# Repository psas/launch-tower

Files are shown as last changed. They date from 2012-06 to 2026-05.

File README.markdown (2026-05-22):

PSAS Launch Tower Computer (LTC)
================================

PSAS has had three generations of launch tower computers:

- [LTC v1 (2005-2012)](http://psas.pdx.edu/Lv2LaunchTowerElectronics/)
   - PC-104+ 486 running Linux 2.4 talking CAN to PIC18F-based boards with relays and analog
   - Lucent "Wavelan" PCMCIA WiFi card
   - 12V SLA battery powered with 30W solar panel
   - Metal IP66 case on independent
- [LTC v2 (2012 - 2014)](http://psas.pdx.edu/GroundTeamHome/launch_tower_v2/)
   - Beagle board talking USB to Phidget relay and analog boards
   - Alpha WiFi board
   - Ethernet umbilical cord
   - 12V SLA battery powered with 30W solar panel
   - Medium sized plastic IP67 enclosure
- LTC v3
   - BeagleBone Black using GPIO and analog mounted on a single custom carrier PCB
   - 14.7V LiPo pack with solar charger.
   - Smaller case

This repo contains everything related to the launch tower computer
(LTC), with the exception of the userspace software, which is
contained in the [launch-tower-comm repo](https://github.com/psas/launch-tower-comm).

Contents
========

- doc
   - Documentation, what there is of it.

- eagle
   - Schematics and PCB layouts, made with [Eagle](http://www.cadsoftusa.com/).

- laser_cut_drawings
   - Line art of the power and ignition boards' mounting panels, suitable for use with a laser cutter.

- ltc3
   - Everything related to the design and manufacture of the third generation launch tower computer, LTC3.

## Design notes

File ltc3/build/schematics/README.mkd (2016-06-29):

# Launch Tower Computer III Schematics

This directory contains PDF schematics for each board in the LTC3
design.

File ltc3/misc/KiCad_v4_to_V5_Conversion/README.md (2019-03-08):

# KiCad v4 to V5 Conversion

This directory contains sed scripts used to convert LTC3's KiCad design
files from v4 to v5.

Conversion is a two-part process:

1. Create a complete sed script.  Start with the "base" sed script
   (suitable for any eeschema v4 files ) by appending rules for the
   conversion of local symbol names::

    cp eeschema_v4_to_v5_base.sed eeschema_v4_to_v5.sed
    (cd ../../kicad/libs/symbols/ && grep \$CMP *dcm) | sed -f make_sed_rules_for_local_symbols.sed >> eeschema_v4_to_v5.sed

2. Convert individual eeschema ``*.sch`` files::

    sed -f eeschema_v4_to_v5.sed $YOUR_EESCHEMA_FILE_HERE > $YOUR_EESCHEMA_FILE_HERE.v5

The resulting output is totally guaranteed to probably not be perfect,
usually because a previously-used stock symbol has changed slightly in
size, default orientation, etc.  Some post-conversion assembly may be
required.

Also note that the above example commands may well need to be adjusted
to suit your working environment ($PWD, etc.)

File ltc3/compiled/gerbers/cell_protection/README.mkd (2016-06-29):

# Cell Protection Gerbers

This directory contains Gerber design files for the LTC3 cell
protection board.

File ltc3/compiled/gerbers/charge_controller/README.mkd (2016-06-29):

# Charge Controller Gerbers

This directory contains Gerber design files for the LTC3 charge
controller board.

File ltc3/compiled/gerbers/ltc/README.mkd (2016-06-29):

# Launch Tower Computer Gerbers

This directory contains Gerber design files for the LTC3 main board.

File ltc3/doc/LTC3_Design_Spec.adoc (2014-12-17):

= PSAS Launch Tower Computer III Design Specification

FIXME: Feel free to make any additions or corrections.

== Abstract

The existing launch tower computer (LTC), the second major design
since the group's founding, is due for an overhaul.  It's only been
two years since LTC II was put into service, but there have been rapid
advances in available off-the-shelf technology, and our understanding
of what we need (and don't want) in an LTC has continued to evolve.

This document should be considered the source of authority for all
questions related to the design and implementation of the LTC III.

== Definitions

Computer::
  The single-board computer that comprises the core of the LTC.

Launch Tower Computer (LTC)::
  The entire system, including the enclosure, the single-board
  computer, the peripherals, etc.

== LTC II Review

=== The Good

* Safety interlocks!

* Solar charging.

* LiPo ignition battery.

=== The Bad

* http://www.phidgets.com/[Phidgets].  Expensive (relatively), fiddly,
  and require their own interface board.  Their software stack is
  thick and troublesome to install.

* The shore power DC-DC converter integrated with the power board was
  sorely inadequate.

* Lead-acid car batteries (LTC II's main power source) are bulky and
  heavy.

* The door covering the side bulkhead (power and arm switches) can't
  be closed when the shorting bar is in place.  The bar has to be
  stored elsewhere when the LTC not in use.

* The PowerPole connectors on the bottom bulkhead are too deeply
  recessed, located too close together, and poorly labeled.

== LTC III Goals

* Simplify!  LTC II has too many circuit boards, too many wires, too
  many everything.  It's difficult to service most of LTC II's
  components without major disassembly.  Peripherals (sensors, relays,
  etc.) should be contained on a single custom PCB.

* Make it smaller.  Reduce the size of the boards, batteries, and
  potentially even the enclosure.

* Replace LTC II's plastic enclosure with a metal enclosure, for
  durability and RFI protection.

* Improve the enclosure-to-tower mounting apparatus;
  make it fast and easy to mount (and dismount) the enclosure to the
  tower (https://en.wikipedia.org/wiki/DIN_rail[DIN rail] mounting (or
  something similar).

* Strive for field-replaceable units (FRU) whenever possible.  FRUs
  can be swapped out with basic tools, in a minimum amount of time.

* Make it user-friendly (i.e., fool-proof).  Any member of PSAS
  should be able to achieve a high-level understanding of the LTC in a
  short amount of time.  Any member should be able to operate, and if
  necessary service, the LTC given suitable documentation.

* Conduct a thermal analysis.  Do we need an active cooling system to
  deal with the heat of a desert launch site?

== Requirements

=== Power Sources

All the ways the LTC can get the juice it needs.

* 12 VDC rail from main batteries.

* 12 VDC rail from photovoltaic panels.

=== Power Supplies

The power rails the LTC provides to its various peripherals.

* 5 VDC rail to power to computer, etc.

* 12 VDC rail to ignition battery charger.

* 24 VDC rail to shore power.

* Several external expansion power connectors; switchable by the
  computer.

=== Sensors

* Voltage sensors for each power rail.

* Temperature sensor for enclosure interior.

* Support for at least four relays.

* External USB-connected WiFi adapter for computer.

* Add second enclosure access panel.  Divide main power switch; and
  ignition arming switch, shorting bar, and fuse into separate panels.

=== User Interface

* Stand-alone voltmeters on the front panel, for each power rail.
  (Stand-alone meters have no dependency on the computer being
  booted.)

* Front panel LEDs indicating the status of each relay, and the
  rocket-ready status.

* Main power switch

* Ignition arming switch.

* Ignition shorting bar.

* Ignition fuse.

* Label all the things!  Components, connectors, switches, oh my!

=== External Connections

* Rocket umbilical.  Connection state should be detectable by the
  computer.

* Away box

* WiFi coax

* Distinct, keyed connectors for each external connection.  There
  should be no way to accidentally connect a data cable to a power
  outlet; or to reverse the polarity of a connector.

* Several Ethernet connectors that provide external access to the
  LTC's internal subnet, for debug and expansion purposes.

* Several expansion trigger switches, for computer control of cameras,
  etc.  Switches short two external inputs together.  Nate proposes
  1/8" phono connectors for these.

* Expansion Ethernet and power connectors can be paired up for use
  with passive PoE injectors, providing single-cable power and network
  support for off-board devices (e.g., weather station).

== Design

TODO: More words, please.

* BeagleBone Black SBC

* BBB flipped upside down and mated to peripheral board via pin
  headers.  A kilt, rather than a cape!

=== Power Sources

=== Power Supplies

=== Ignition Subsystem

=== Networking

* Internal Ethernet switch.

== References

http://kilobaser.com/blog/2014-07-15-beaglebone-black-gpios["BeagleBone
Black GPIOs"], KiloBaser.

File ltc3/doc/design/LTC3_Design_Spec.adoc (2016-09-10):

= Portland State Aerospace Society Launch Tower Computer 3 Design Specification
PSAS Avionics Team <psas-avionics@lists.psas.pdx.edu>
v0.5, 14 July 2016: DRAFT

:imagesdir: ./images

== Summary

This document is the source of authority for all questions related to
the design and implementation of the third PSAS Launch Tower Computer
(LTC3).  If the design of LTC3 doesn't conform to this document, then
either the design is incorrect, or the document needs to be updated!

== Power

=== Sources
LTC3 will get its power from a bench power supply while in the lab,
and photovoltaic panels and batteries while in the field.

Minimum input voltage is determined by the DC-DC converter supplying
the 19 VDC rail, which requires an overhead of 4 VDC.  At minimum, a
24 VDC supply capable of sourcing at least TODO 10 amps is required.
footnote:[Refer to Texas Instruments PTN78020[WH\] datasheet, Aug.
2011, page 10, "Input Voltage Considerations"]

=== Battery
LTC3 uses a 28.8V, 8s2p LiPo battery pack.  The 28.8V nominal voltage
enables the use of buck converters on all three DC power rails.
Configurable buck converters are cheap and plentiful, and have higher
efficiencies than the boost converters.  Furthermore, the 8s2p
configuration enables us to charge-balance individual cells.  The
downside is the need for a custom charging circuit, as most
off-the-shelf chargers are designed for 12V nominal MPPT and 4s cell
configurations.

==== TODO
* Based on assumptions: 90% efficiency, calc. 96W of power (a
  conservative estimate), 4 hours pure battery, we need a capacity of
  13.2Ah at 28.8V nominal.
* An 8s2p final configuration of 6.7 Ah cells would get
  us into our 4 hours.

==== Charge Controller
LTC3 uses the Linear Technologies LT8490, a switching buck/boost
regulator that integrates a charger and solar MPPT.  It is robust and
inexpensive.  Implementation of circuits based on the LT8490 are
somewhat complicated, but are a big win in terms of cost and system
flexibility.  The LT8490 can be powered with a wide range of input
voltages.  A single connctor can be used for either the solar panels
or 12V bench power supplies.

==== Battery Management and Cell Protection
LiPo cell protection is provided by a Texas Instruments bq77PL900
("bq").  The bq performs both battery balancing and protection
for up to 10 lithium-polymer cells.  Cell balancing and protection
prevent over-charging and -discharging of cells, giving the batteries
extra run time and lifespan.  It also prevents the overheating of
cells (a fire hazard), and prevents early capacity degradation.

===== Basic Function
The bq utilizes two different PMOS devices, which are turned on and
off by a microcontroller in the chip.  The bq senses battery cell
voltages through its VC pins (VC1-VC10).  When the battery's voltage
grows too high, the bq applies a voltage to the gates of the PMOS CHG
FETs, whose body diodes then prevent current from passing from the
input to the battery.  Likewise, when the battery's voltage drops too
low, the bq applies a voltage on the gates of the DSG PMOS FETs, whose
body diodes prevent current from passing from the battery to the load.
The charge pump built into the bq allows gate voltages to become high
enough for the CHG and DSG FETs to switch on and off.

===== Active Balancing
The bq uses active balancing in its design.  To do this, an integrated
NMOS in the chip is connected between two of the VC pins and turns on
when a certain voltage drops across it.  As a result, if one cell's
voltage is too much greater than another, the voltage drop across the
NMOS pushes current to the adjacent cell, and so on and so forth.  An
external 500Ω current-limiting resistor is used in conjunction with a
0.1μF filter capacitor.

===== Temperature Sensing
The temperature sensing feature of our design revolves around the TOUT
and TIN pins on the bq.  A voltage divider network is put in parallel
with a 10kΩ thermistor, which is taped to the battery pack.  The
thermistor's resistance decreases with increasing temperature (NTC).
When the battery pack gets hot, the voltage on the TIN pin becomes
low, turning off both the DSG and CHG FETs.  This prevents current
from flowing into our out of the battery, allowing it time to cool
off.  Once the temperature has stabilized, the bq resumes its regular
function.

===== Zero-Volt Charging
The zero-volt charging in our design is driven by another PMOS device
via the general-purposed open-drain ("GPOD") pin.  When voltage drops
below the supply voltage of the bq, the 0-V/precharge is enabled.
When this happens, the GPOD pin drives the 0-V/precharge FET (Q306 in
the LTC3 schematic).  When this FET is turned on, the CHG FET is
bypassed and current passes through the GPOD FET, allowing the battery
to charge.  When the voltage reaches a sustainable level for the bq to
operate, the GPOD FET is turned off and the CHG FET takes over.

===== Shutdown Mode
When undervoltage is detected, the bq goes into shutdown mode.  In
this mode, the DSG FET is turned off and all functions of the bq
cease.  To exit shutdown mode, a voltage greater than V~STARTUP~ must
be applied on the PACK+ pin.  This can be done in our system by
applying an output voltage from the LT8490 onto the PACK+ pin of the
bq.

=== DC Rails
LTC3 has three DC power rails:

* 5 VDC, for the Beaglebone, cape, and supporting logic
* 12 VDC, for the Ethernet switch and external device support
* 19 VDC, for rocket shore power

DC power rails are supplied by Texas Instruments PTN78020 switching
regulators.  The PTN78020 is a wide-input, wide-output, adjustable 6 A
regulator.  A PTN78020W converter is used for the 5 VDC rail;
PTN78020H converters are used for the 12 VDC and 19 VDC rails.

Based on the temperature derating curves in the PTN78020 datasheet
(rev. Aug. 2011), our worst case scenario is 4.0A load on the 12V DC
rail.  Fig. 21 in the datasheet indicates that the maximum ambient
temperature for such a load is approximately 55 °C.

.LTC3 DC Power Rails
[width="25%",frame="topbot",options="header"]
|===============================================
| V~out~ | I~min~ | I~typ~ | I~max~ | Part Num.
| 5.0    | ?      | 1.0    | 2.0    | PTN78020W
| 12.0   | ?      | ?      | 5.0    | PTN78020H
| 19.0   | ?      | 3.0    | 4.0    | PTN78020H
|===============================================

== Ignition Subsystem

The ignition system functions off three different relays.  The rocket,
which is connected with an umbilical cord, tells the LTC it is
prepared to launch by sending a "ROCKET_READY" signal to the LTC.
This activates a solid state relay (IC601) which pushes signal to the
following AND gate.

When the LTC sees the rocket ready signal and shore power, after a 5
second delay the second relay (K601) is triggered. Additionally, an
LED lights up indicating the rocket is "ready to launch," and assuming
the relay locks, the first light on the "BAKERCON" indicator will
light up.

The third relay is activated by the "ROCKET_IGNITE" pin from the
beaglebone on the LTC3. At this point the second light on the BAKERCON
idicator is lit.  When this signal is active, the third relay (K602)
closes and the system goes through a breaker arm, switch, and banana
jack to ensure launch is desired. When these three are connected, the
third and final BAKERCON indicator light is active.

The final step to launching the rocket is connecting the short-bar,
known as the launch key, to the away box.  When all of these
conditions have been met, the rocket will launch.

== Computer

The heart of LTC3 is a BeagleBone Black (BBB) single-board computer.

The BBB interfaces with the main board via a pair of 46-pin headers.
The main board appears to the BBB as a standard
http://beagleboard.org/cape["cape"].  The main board is on the bottom,
with the BBB mounted on top, upside-down.

=== Cape EEPROM Contents
TODO

== Sensors

LTC3 contains sensors to monitor the voltage and current sourced from
the photovoltaic panels; sourced from the main battery; and sunk on
the 5 VDC, 12 VDC, and 19 VDC rails.

Sensing of voltage, current and temperature alike is accomplished with
a pair of http://cds.linear.com/docs/en/datasheet/2991fd.pdf[Linear
Technologies LTC2991] _Octal I2C Voltage, Current, and Temperature
Monitor_ ICs.  One IC is dedicated to the LTC3's power sources, the
other to its sinks.  The ICs interface with the BeagleBone via an I2C
bus.

The temperature sensor integral to each LTC2991 will be used to
monitor the LTC3 main board.  An MMBT3904 NPN BJT connected to the
first LTC2991 (same IC used to monitor the power sources' voltage and
current) will be used to monitor the temperature of the main battery.

== Networking

* Internal Ethernet switch.

== External Device Support

LTC3 provides power and trigger support for four external devices
(e.g., cameras).

=== Power
Power is supplied through two-terminal Anderson Powerpole connectors,
available from the exterior of the LTC enclosure.  Current to each
connector is limited by a 2 A PPTC (PolyFuse).

Each power connector is controlled independently by the computer.
Photorelays, driven via GPIO through a MOSFET, are used to switch the
12 VDC rail to "Eurostyle" connectors mounted to the mainboard.
Common, 16-gauge stranded copper wire carries current from the
on-board connectors to the exterior-facing Powerpoles.

=== Triggers
Triggering is supplied through two-terminal TODO-CONNECTOR_TYPE
connectors, available from the exterior of the LTC enclosure.  Current
to each connector is limited by a 500mA A PPTC (PolyFuse).

Each trigger connector is controlled independently by the computer.
Photorelays, driven via GPIO through a MOSFET, are used to switch
either ground, or the 5 VDC rail, to "Eurostyle" connectors mounted to
the mainboard.  An on-board three-pin header is jumpered accordingly
to select the signal, whichever suits the device being triggered.

== User Interface

=== BAKERCON Hazard Gauge
Indicates at a glance how close ignition battery power is to the
rocket ignition outlet (to which the away box is connected).  Three
super-bright LED indicators are mounted to the enclosure exterior.
The first, yellow, lights when the ignition battery relay closes.  The
second, also yellow, lights when the rocket ignition relay closes.
The third, red, lights when power reaches the outlet.

The ignition sub-system is still fully functional when the 12V and 19V
supplies are disabled.  Thus, the BAKERCON is powered off of the 5V
supply.

== Physical

=== Printed Circuit Board
Trace widths must be sufficient minimize circuit impedance, and to
limit temperature rise.  Assume a maximum ambient temperature
(enclosure interior) of 60°C.  Maximum trace temperature rise should
be no more than 20°C.

=== External Connectors
IDEA: Powerpole connectors are mounted to the enclosure with
http://www.portableuniversalpower.com/anderson-autogrip/[Anderson
AutoGrips].  They're robust and inexpensive.

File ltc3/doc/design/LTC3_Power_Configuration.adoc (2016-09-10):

Does the LT8490 need to be reconfigured in order to take different
nominal input voltages?
  - pg. 14 - VINR needs to be grounded when the chip is getting direct
    DC input. (pg. 14) When panels are used, it needs to be hooked up
    to a resistor network to measure panel voltage.  This is
    implemented on pg. 35 - protection diodes are used to insulate VDC
    and VPanel, and a transistor shorts VINR when VDC is turned on.
  - We can ensure that no one uses the Lab and Panel supplies at the
    same time by just having a physical sliding cover.
	- DC current limiting for lab power

What configuration options does the LT8490 have? How should they be
configured?
  - Vmax selection - Based on the larger of panel Voc Max and DC max,
    we calculate an impedence network (pg. 14).  Minimum ckt input
    voltage is based on the selected Vmax; the lab power input and
    solar input both must exceed this level for efficient charging.
    (pg. 15).
	- Low-power mode - pg. 15
  - Simultaneous charging + discharging (in-situ; pg. 16) 
		- load connected directly across the battery terminals
    - disable charging time limits (CHARGECFG2 pin) 
    - the battery may draw below safe levels if it is charging and
      discharging simultaneously; build in protections?
  - Stage 2 charging threshold (pg. 17-18) - typically above nominal
    Vbatt; for LiPo cells this is usually 4.2V for 3.6V cell
    - Stage 3 is usually disabled for LiPo; the Stage 2 threshold is
      the most important limit for LiPo charging
	
- IMON_OUT, IMON_OUT capacitance (pg. 19, 20) - higher values reduce
  inductor current overshoot; lower values reduce ripple and give
  better ADC measurements. Need to separate pole at IMON_OUT from pole
  at Vc pin. Suggested value: 4.7 to 22nF
  - Input current limiting (pg. 19) should be panel max + 20%, but not
    dramatically higher than rated input
	- CHARGECFG1 options: (pg.20)
		- Temperature-compensated voltage limits
		- Enable/disable stage 3 (not typically used for LiPo)
    - For LiPo: Non-temperature-compensated, stage 3 disabled =
      grounded
  - CHARGECFG2 options: (pg. 22)
    - Enable/disable charge time limits: time limits not recommended
      for LiPo
    - Width of valid temp ranges (ratio > or < 0.5)
    - For LiPo: Narrow valid temp range, no time limits = grounded
  - Status/Fault LED configuration (pg. 26)
		- Use a resistor to limit STATUS current
		- FAULT self-limits on its own
		- Configure BB to interpret status/fault signals (pg. 25)
		- For our config: use resistor network as in Fig. 18
	- Switching configuration (pg. 29)
    - MODE pin above 2.3V = discontinuous conduction mode (DCM)
    - MODE below 0.4V = automatic CCM/DCM mode switching, automatic
      EXTVcc disconnect
    - For our config: tie MODE low - we typically want CCM
	- Low power mode (pg. 30)
		- Disabling: Rnlp can be connected between to FBIR.
		- For our config: no reason to disable low-power mode
	- Feedback resistor disconnect (pg. 31)
    - For our config: Feedback resistor disconnect is probably
      unnecessary for our application
    - We want voltage sensing even when batteries are not charging
    - Circuit as in fig. 26
	- EXTVcc disconnect mode (pg. 32)
    - For our config: EXTVcc disconnect is probably unnecessary
		- EXTVcc power draw is very low relative to our batteries
	- Remote batt V sensing (pg 32)
		- intended for low-voltage batteries charging at high currents
		- For our config: Not necessary.
	- Hot plugging (pg. 35)
    - We can either use the remote batt V sensing setup or use a
      staggered connector type
    - Word of god: don't worry about it for our application

- Inductor selection: see LT8705 datasheet for consideration (pg. 23)

- Board Layout checklist: see LT8705 datasheet (pg. 35)

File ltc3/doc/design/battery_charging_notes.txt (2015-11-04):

	-->

---------------------------------------------------------------------------

Welcome to Andy's Awesome program!  I hope you enjoy your time here!

---------------------------------------------------------------------------

What is maximum voltage that the solar panel will give?: 21.7

What is the stage 2 constant voltage you want for the batteries?: 33.6

What is the maximum input current from the solar panel?: 2.4

What is the maximum charging current?: 11.4

What is the maximum trickle current value?: 3

What would you like Rfbout2 to be? (choose between 4.99k - 49.9k ohms): 7000

What would ou like the switching frequency to be?:  250000

---------------------------------------------------------------------------------------------------------

Based on the specifications, the exact values you want should be:

Rfbin1 = 94725.966280

Rfbin2 = 7731.641101

Rdaci1 = 3318.425570

Rdaci2 = 16592.127852

Cdaci = 3.013477E-07

Rfbout1 = 203920.989595

Rfbout2 = 7000.000000

Rdac01 = 7899.283126

Rdac02 = 39496.415628

Cdac0 = 2.531875E-07

Rsense1 = 0.021042

Rsense2 = 0.004360

Rimonout = 92362.173038

Riow = 32975.744156

Rior = 3010.000000

---------------------------------------------------------------------------------------------------------

Based on the specifications, here are the closest real resistor values you can use:

Rfbin1REAL = 95300

Rfbin2REAL = 7680

Rdaci1REAL = 3320

Rdaci2REAL = 16500

CdaciREAL= 3.3E-07

Rfbout1REAL = 200000

Rfbout2REAL = 7150

Rdac01REAL = 8050

Rdac02REAL = 40200

Cdac0REAL = 2.7E-07

Rsense1REAL = 0.021

Rsense2REAL = 0.00432

RimonoutREAL = 93100

RiowREAL = 33200

RiorREAL = 3010

---------------------------------------------------------------------------------------------------------

Choose an inductor greater than 3.11562e-06 H

---------------------------------------------------------------------------------------------------------

-->

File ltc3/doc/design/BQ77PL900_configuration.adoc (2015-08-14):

-Eight-cell configuration: CNF2 and CNF0 shorted, CNF1 connected to VLOG through a 10kOhm resistor
-ZEDE to GND - normal operation for detection delay

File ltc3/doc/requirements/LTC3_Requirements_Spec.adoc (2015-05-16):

= Portland State Aerospace Society Launch Tower Computer III Requirements
PSAS Avionics Team <psas-avionics@lists.psas.pdx.edu>
v0.1, 27 January 2015: DRAFT

:imagesdir: ./images

== Summary

The launch tower computer (LTC) is an integral component in the
Portland State Aerospace Society (PSAS) launch vehicle complex.  It is
responsible for providing shore power to the rocket while it remains
on the launch pad; manages the ignition safety interlock system; and
ignites the rocket motor at launch time.

The existing launch tower computer, the second major design
since the founding of the http://psas.pdx.edu/[Portland State
Aerospace Society] (PSAS), is due for an overhaul.  It's only been two
years since LTC II was put into service, but there have been rapid
advances in available off-the-shelf technology, and our understanding
of what we need (and don't want) in an LTC has continued to evolve.

This document is the source of authority for all questions related to
the requirements of the LTC III.  If the document does not conform to
the known requirements, then either the requirements are incorrect, or
the document needs to be updated!

== LTC II Review

=== The Good
* Smaller and less heavy than LTC I

.The guts of LTC I
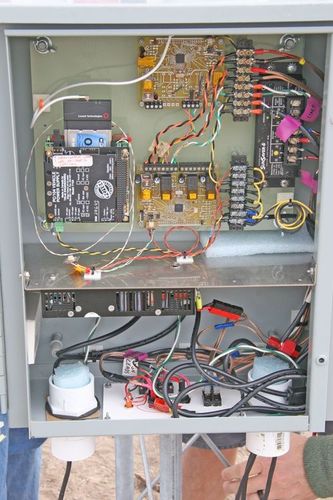
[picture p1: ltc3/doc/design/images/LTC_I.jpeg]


* Safety interlocks!

* Solar charging.

* LiPo ignition battery.

.LTC III ignition board and LiPo battery pack.
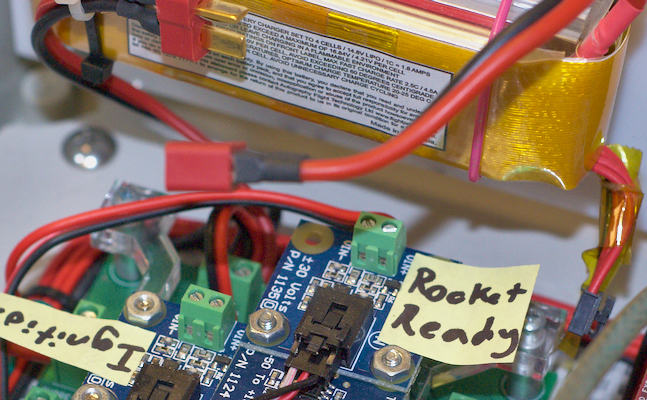
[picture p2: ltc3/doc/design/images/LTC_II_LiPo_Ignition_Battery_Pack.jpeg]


=== The Not So Good

* While smaller and lighter than LTV v1, still big and bulky and a
  pain to carry around.

* Complicated, heavily mod-wired, and difficult-to-trace wires all
  conspire to make debugging a real chore.

.The guts of LTC II
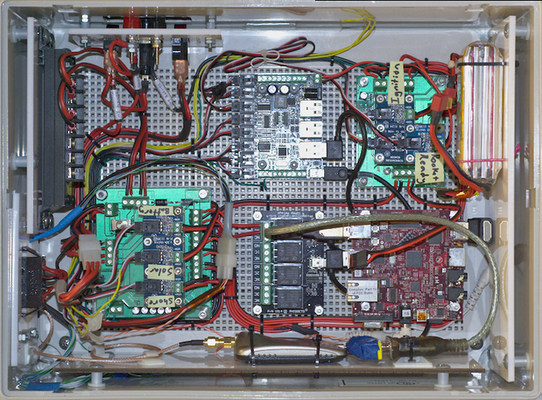
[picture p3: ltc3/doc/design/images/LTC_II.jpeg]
Photo of the interior of LTC II


* The shore power DC-DC converter integrated with the power board was
  sorely inadequate.

.LTC II power board.
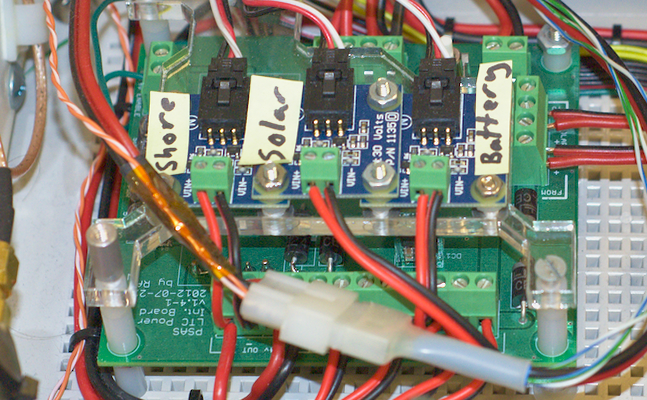
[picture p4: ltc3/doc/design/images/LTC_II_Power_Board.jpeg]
Photo of LTC II's power supply board.


* Lead-acid car batteries (LTC II's main power source) are bulky and
  heavy.

* http://www.phidgets.com/[Phidgets].  Expensive (relatively), fiddly,
  and require their own interface board.  Their software stack is
  thick and troublesome to install.

.LTC II Phidgets interface board.
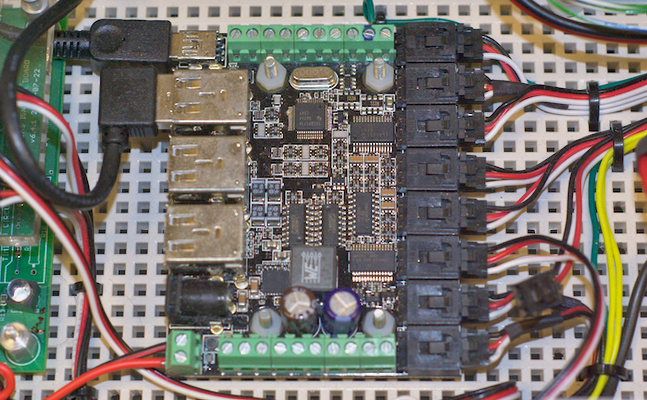
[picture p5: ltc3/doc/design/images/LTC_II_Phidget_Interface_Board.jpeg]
Photo of LTC II's Phidgets interface board.


* The door covering the side bulkhead (power and arm switches) can't
  be closed when the shorting bar is in place.  The bar has to be
  stored elsewhere when the LTC not in use.

.LTC II bulkhead access door.
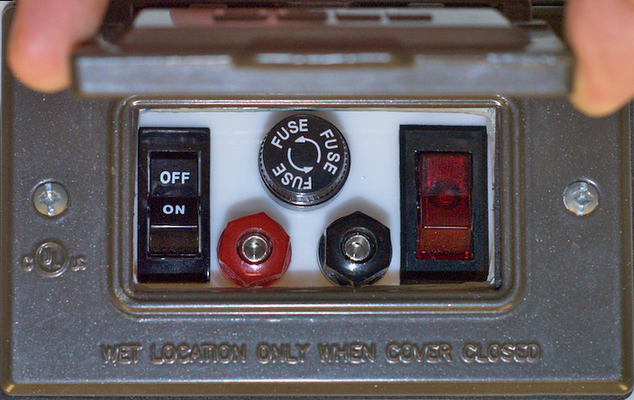
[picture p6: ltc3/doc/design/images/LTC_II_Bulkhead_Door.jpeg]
Photo of LTC II's bulkhead access door.


* The PowerPole connectors on the bottom bulkhead are too deeply
  recessed, located too close together, and poorly labeled.

.LTC II external power connectors.
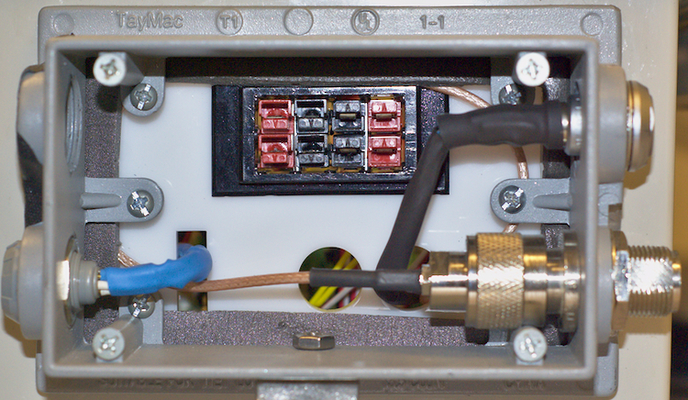
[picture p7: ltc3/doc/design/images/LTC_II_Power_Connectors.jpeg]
Photo of LTC II's power connectors.


== Goals

* Simplify!  LTC II has too many circuit boards, too many wires, too
  many everything.  It's difficult to service most of LTC II's
  components without major disassembly.  Peripherals (sensors, relays,
  etc.) should be contained on a single custom PCB.

* Make it smaller.  Reduce the size of the boards, batteries, and
  potentially even the enclosure.

* Use commercial, off-the-shelf (COTS) hardware whenever possible.
  COTS hardware will (ideally) have been subjected to far more
  engineering scrutiny than we'll be able to afford.

* Strive for field-replaceable units (FRU) whenever possible.  FRUs
  can be swapped out with basic tools, in a minimum amount of time.

* Make it user-friendly (i.e., fool-proof).  Any member of PSAS
  should be able to achieve a high-level understanding of the LTC in a
  short amount of time.  Any member should be able to operate, and if
  necessary service, the LTC given suitable documentation.

* Conduct a thermal analysis.  Do we need an active cooling system to
  deal with the heat of a desert launch site?

* Improve the enclosure-to-tower mounting apparatus;
  make it fast and easy to mount (and dismount) the enclosure to the
  tower (https://en.wikipedia.org/wiki/DIN_rail[DIN rail] mounting (or
  something similar).

* Optional: Replace LTC II's plastic enclosure with a metal enclosure, for
  durability and RFI protection, without sacrificing light weight.

== Requirements

=== Power
The LTC will receive power from the following external sources:

* Photovoltaic (PV) panels
** Panels provide 10.0/12.0/17.0 VDC (min., nominal, max.)

* Lab power connection
** Used when power from PV panels is not available.
** Maximum 24 VDC
** Suggested: use a ThinkPad switching "pregnant snake" power supply
   (19 VDC, several amps).

The LTC must include a bank of internal LiPo cells ("main" batteries):

* Capacity must be sufficient to provide power to both internal and
  external loads (approx. 4 AH).
* Batteries must be charged by available external power.

The LTC must provide power to the following sub-systems:

* Computer
** 5 ±0.25 VDC at 1.0 A max. (BeagleBone Black spec.)

* Rocket
** Shore power
** 19 VDC @ 4 A

* Ignition, etc. control board(s)
** 5 VDC.

* Ignition battery charger
** 12 VDC, direct from PV panels
** _Not_ integral to the LTC main board
** COTS hardware strongly preferred

* Several external expansion devices
** Via external connectors
** Switchable by the computer

=== Computer
* COTS single-board computer (SBC).
* Able to run a current Debian "stable" Linux system.
* Strongly prefer to keep the existing BeagleBone Black.
* At least one 100MB Ethernet port.
* At least two USB 2.0 ports.

=== Network

* WiFi connection to Launch Control.

* Internal Ethernet switch
** Able to support the computer; rocket; several external hosts
   (debug, expansion peripherals)

=== Relays

* Ignition

* Rocket ready
** Controlled by the rocket, independent of the LTC

* Expansion peripherals
** Switch across input pair (no power)
** Opto-isolated

=== Sensors

The LTC must provide sensors to support the following:

* Voltage on each power rail

* Current consumption
** PV panels
** Main battery
** Rocket shore power

* Temperature
** Main board
** Main battery pack
** Enclosure interior

* Rocket-ready status

* Umbilical connection state

* Ignition fuse state

=== User Interface

* Main power switch

* Ignition arming switch.

* Ignition shorting bar.

* Ignition fuse.

* Front panel display with "vital signs"
** Activated by momentary push-button.
** Suggested: a display panel driven by the computer.  Panel should be
   easily visible in broad daylight (e.g., transflective grayscale LCDs).
   Panel would need to be protected from impact damage (i.e., mounted
   behind an acrylic window).

* Front panel status LEDs
** Relays open/closed
** Rocket ready/not-ready
** External triggers activated
** Must be daylight-readable (shrouded?)

* Label all the things!  Components, connectors, switches, oh my!

=== External Connections

* Power In
** solar panels
** lab (AKA "shore shore")

* Rocket umbilical
** Ethernet, shore power, rocket-ready

* Away box

* WiFi coax to external antenna

* Expansion support
** Power connectors, connected directly to main battery rail.

** Several Ethernet connectors that provide external access to the
   LTC's internal switch, for debug and expansion purposes.

** Several expansion trigger switches, for computer control of cameras,
   etc.  Switches short two external inputs together.  Nathan proposes
   1/8" phono connectors for these.

** Expansion Ethernet and power connectors can be paired up for use
   with passive PoE injectors, providing single-cable power and network
   support for off-board devices (e.g., weather station).

* Distinct, keyed connectors for each external connection.  There
  should be no way to accidentally connect a data cable to a power
  outlet; or to reverse the polarity of a connector.

=== Enclosure

* Metal
** More robust than plastic.
** Provides greater protection from EMI than plastic.

* Width no greater than the tower it mounts to.

* Able to lay flat on a tabletop.

* Improved mounting apparatus
** Able to be mounted by a single individual.
** Tool-free, preferably.

=== Wish List

* Andrew strongly suggests a single-board LTC3.
** Lots of Maxim Test Points along traces between sub-systems.

* Prototyping area on main board
** 0.1" hole grid; off-board connectors

* Multiple backup LTCs.

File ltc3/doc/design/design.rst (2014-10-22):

==============================================
PSAS Launch Tower Computer III Design Overview
==============================================

FIXME: Feel free to make any additions or corrections.

Abstract
========

The existing launch tower computer (LTC), the second major design
since the group's founding, is due for an overhaul.  It's only been
two years since LTC II was put into service, but there have been rapid
advances in available off-the-shelf technology, and our understanding
of what we need (and don't want) in an LTC has continued to evolve.

LTC II: Pro and Con
===================

The Good
--------

* Safety interlocks!
* Solar charging.
* LIPO ignition battery.
* I/O devices are almost all USB-based.  *In situ* software
  development is not confined to the LTC's mainboard, but rather can
  take place on any Linux system equipped with USB and a comparable
  Phidgets kit.

The Bad
-------

* Peripherals comprised of multiple custom PCBs, each layered with a
  variety of Phidget-based sensors.
* Phidgets.  Expensive, fiddly, and require their own interface board.
  Their software stack is thick and troublesome to install.
* Difficult to service various components without major disassembly of
  entire LTC.  Wires everywhere!

LTC III Goals
=============

* Simplify.
* Reduction in size: boards, batteries, enclosure.
* Field-replaceable components that can be swapped out in a reasonable
  amount of time.
* Backups for every major component.  Two is one and one is none!
* User-friendly.  Any member of PSAS should be able to achieve a
  high-level understanding of the LTC in a short amount of time.  Any
  member should be able to service the LTC given suitable
  documentation.

Design Overview
===============

* BeagleBone Black SBC
* Peripherals (sensors, relays, etc.) contained on a single custom
  PCB.
* BBB flipped upside down and mated to peripheral board via pin
  headers.  A kilt, rather than a cape!
* Replace lead-acid (car) batteries with high-capacity LiPo cells.
* Use a battery module in common with the rocket.
* Improved enclosure-to-tower mounting apparatus.
* Detectable rocket umbilical connection state.
* Improved external connectors (more robust).
* Improved labeling of various components, connectors, switches, etc.
* Thermal analysis!

External Interface
------------------

* Rocket umbilical
* Away box
* WiFi coax
* Power + Ethernet spare (future capacity)
* Debug Ethernet
* Camera triggers

Design Details
==============

Power Distribution Subsystem
----------------------------

* Solar power in
* Battery charger
* Main battery
* Ignition battery

Ignition Subsystem
------------------

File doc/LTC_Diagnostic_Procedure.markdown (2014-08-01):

# Launch Tower Computer Diagnostic Test Procedures

## Initial Setup

1. Disconnect
  * R± M± S T Q±
  * I± J± K± L±
    * All of these don’t connect devices like batteries and solar
      panel to the exterior connection.
  * N (to battery) O (to charger)
2. S2 to “OFF”

## Test Main Power Switch

1. S2 to “OFF”
2. Continuity test across both H points
  * [PASS] Have NO continuity across points
  * [FAIL] Have continuity across points
3. S2 to “ON”
4. Continuity test across both H points
  * [PASS] Have continuity across points
  * [FAIL] Have NO continuity across points
5. S2 to “OFF”

## Test Solar Panel Connection And Lights
	
1. S2 to “OFF”
2. Connect 9-16 VDC (Vinput) to J±
  * [PASS] L1 light is ON
  * [FAIL] L1 light is OFF
3. Depress and hold S1
  * [PASS] L1 light is OFF
  * [FAIL] L1 light is ON
4. S2 to “OFF”

## Test System Battery Connection And Lights

1. S2 to “OFF”
2. Connect 9-16 VDC (Vinput) to I± or L±
  * [PASS] L2 light is ON
  * [FAIL] L2 light is OFF
3. S2 to “OFF”
4. S2 to “ON”
  * [PASS] L3 and L4 and L5 light is ON
  * [FAIL] L3 and L4 and L5 light is OFF
5. S2 to “OFF”

## Test Power Conversion

1. S2 to “OFF”
2. Connect 9-16 VDC (Vinput) to I± or L±
3. S2 to “ON”
4. Voltage Check: A± B± C± D± E± F±

       | A± and B±        | C± and D±   | E± and F±
-------|------------------|-------------|------------
[PASS] | (Vinput) ± .02 V | 5 V ± .02 V | 24 V ± .02V
[FAIL] | != PASS          | != PASS     | != PASS

5. S2 to “OFF”

## Test Phidget Board

1. S2 to “OFF”
2. Connect: M±
3. S2 to “ON”
4. Voltage Check: M±
  * [PASS] Voltage = (Vinput) ± .02 V
  * [FAIL] Voltage ! = (Vinput) ± .02 V
  * Note: OK if L5 goes out. This indicates Phidget board has turned
    off 24 V converter.
5. S2 to “OFF”

## Test Ignition Board

### Board Power

1. S2 to “OFF”
2. Connect: Q±
3. S2 to “ON”
4. Voltage Check: Q±
  * [PASS] Voltage = 5V ± .02V and L6 is ON
  * [FAIL] Voltage != 5V ± .02V or L6 is OFF
5. S2 to “OFF”

### Shore Power

1. Disconnect: M±
2. Connect: R+
3. S2 to “ON”
4. Voltage Check: R+ / Q-
  * [PASS] Voltage = 24V ± .02V and L5 is ON
  * [FAIL] Voltage != 24V ± .02V or L5 is OFF
5. S2 to “OFF”
6. Re-Connect: M±

### Ignition Battery

NEED PROCEDURE HERE

## Test Ignition Battery Charger

1. S2 to “OFF”
2. S2 to “ON”
3. Voltage Check: S (positive tip)
  * [PASS] Voltage = (Vinput) ± .02V
  * [FAIL] Voltage != (Vinput) ± .02V
4. Connect: S
  * [PASS] Battery charger turns on
  * [FAIL] Battery charger does NOT turn on
  * If charger display shows “Er2”, the input voltage on S is greater
    than the 16V maximum input of charger.
5. S2 to “OFF”

## Test Beagleboard

1. S2 to “OFF”
2. S2 to “ON”
3. Voltage Check: T (positive tip)
  * [PASS] Voltage = 5V ± .02V
  * [FAIL] Voltage != 5V ± .02V
4. Connect: T
  * [PASS] L7 is ON and L8 and L9 start flashing
  * [FAIL] L7 is OFF or L7 is RED
  * Failure at this stage may indicate the polarity is revered on
    connection
4.  Let computer boot, connect to it, and power down the board
    normally.
  * At this stage it may not be a good idea to turn S2 to “OFF”
    because it could corrupt the BeagleBoard image.
5. S2 to “OFF”

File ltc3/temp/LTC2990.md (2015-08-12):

# LTC299x Notes

There's a kernel driver project for the LTC2990:
https://github.com/topic-embedded-products/kernel-module-ltc2990.git

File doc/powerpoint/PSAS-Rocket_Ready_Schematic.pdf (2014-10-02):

# PSAS Rocket Ready Schematic

## Original Circuit By: Andrew Greenberg

## Created By: Richard Witherspoon Created On: May 28th, 2012

## Updated By: Richard Witherspoon Updated On: May 30th, 2012

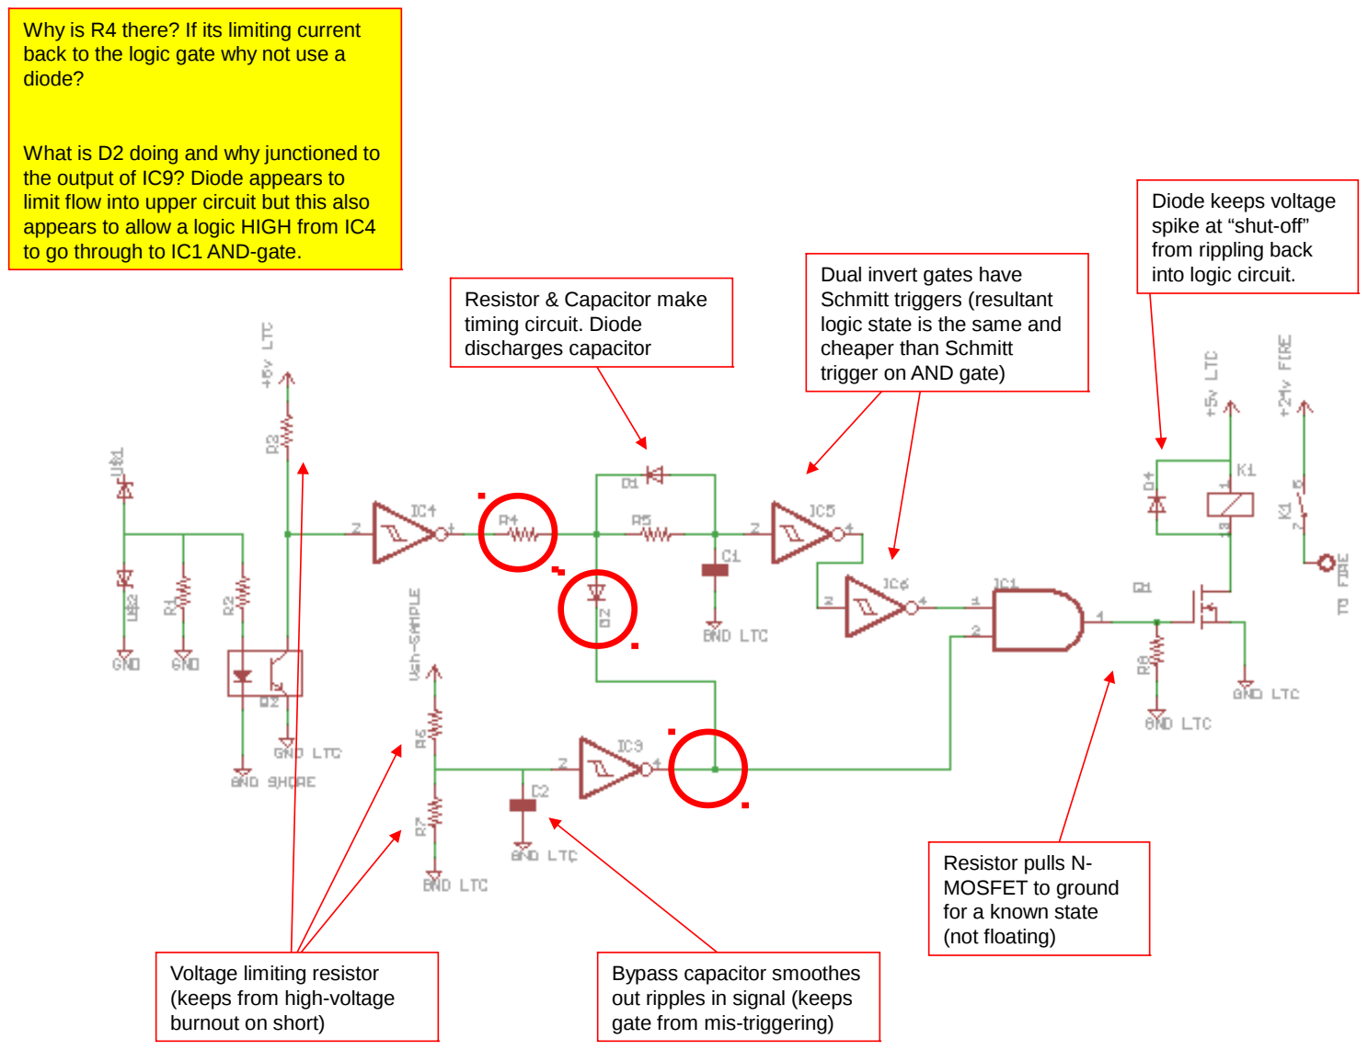
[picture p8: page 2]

Bypass capacitor smoothes
out ripples in signal (keeps gate from mis-triggering)

Resistor pulls N-MOSFET to ground
for a known state
(not floating)

Dual invert gates have
Schmitt triggers (resultant logic state is the same and cheaper than Schmitt
trigger on AND gate)

Resistor & Capacitor make
timing circuit. Diode
discharges capacitor

Diode keeps voltage
spike at “shut-off”
from rippling back
into logic circuit.

Voltage limiting resistor
(keeps from high-voltage
burnout on short)

Why is R4 there? If its limiting current back to the logic gate why not use a diode?

What is D2 doing and why junctioned to the output of IC9? Diode appears to limit flow into upper circuit but this also appears to allow a logic HIGH from IC4 to go through to IC1 AND-gate.

# MODIFIED CIRCUIT

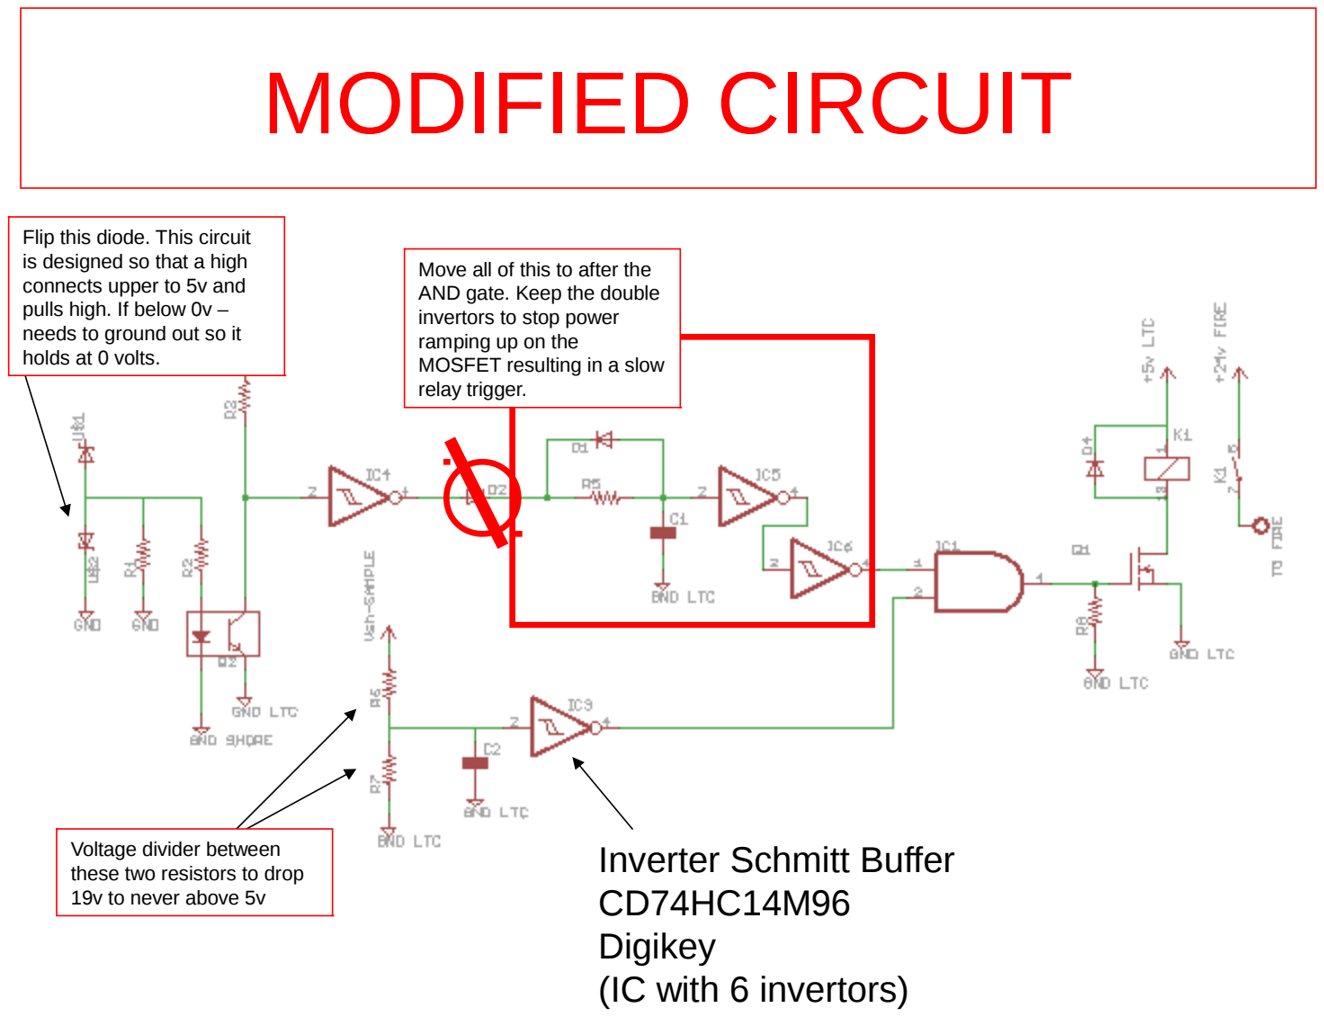
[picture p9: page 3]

Move all of this to after the AND gate. Keep the double
invertors to stop power
ramping up on the
MOSFET resulting in a slow relay trigger.

Voltage divider between
these two resistors to drop 19v to never above 5v

Flip this diode. This circuit is designed so that a high connects upper to 5v and
pulls high. If below 0v –
needs to ground out so it
holds at 0 volts.

# Inverter Schmitt Buffer CD74HC14M96 Digikey (IC with 6 invertors)

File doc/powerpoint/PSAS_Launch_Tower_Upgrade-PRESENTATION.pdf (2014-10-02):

## PSAS Launch Tower Upgrade REVIEW PRESENTATION

## Launch Tower Goals

- Any Linux computer put as controller.
- I/O management through USB external to control computer.
- Acquisition of environmental conditions (wind, temperature, humidity)
- Smaller tower box (reduction of 50% weight)
- Visual indication of system health @ launch tower
- Visual ground control software
- Provide future capabilities
– Trigger video acquisition of takeoff.
– Addition of more sensors

## Old vs. New System

- Unreliable wireless
- System weight
- System size
- Ign. battery weight
- x86 and PIC boards
lost in time
- Questionable
reliability
- New wireless card
- Lighter
- Smaller
- LIPO Launch battery
- New COTS system
- Designed to be
reliable

## How Reach Goals

- Smaller Computer
– Beagleboard
- Data Acquisition
– Phidgets
- System Health
– Power Interface Board
– Ignition Board

## System Block Diagram

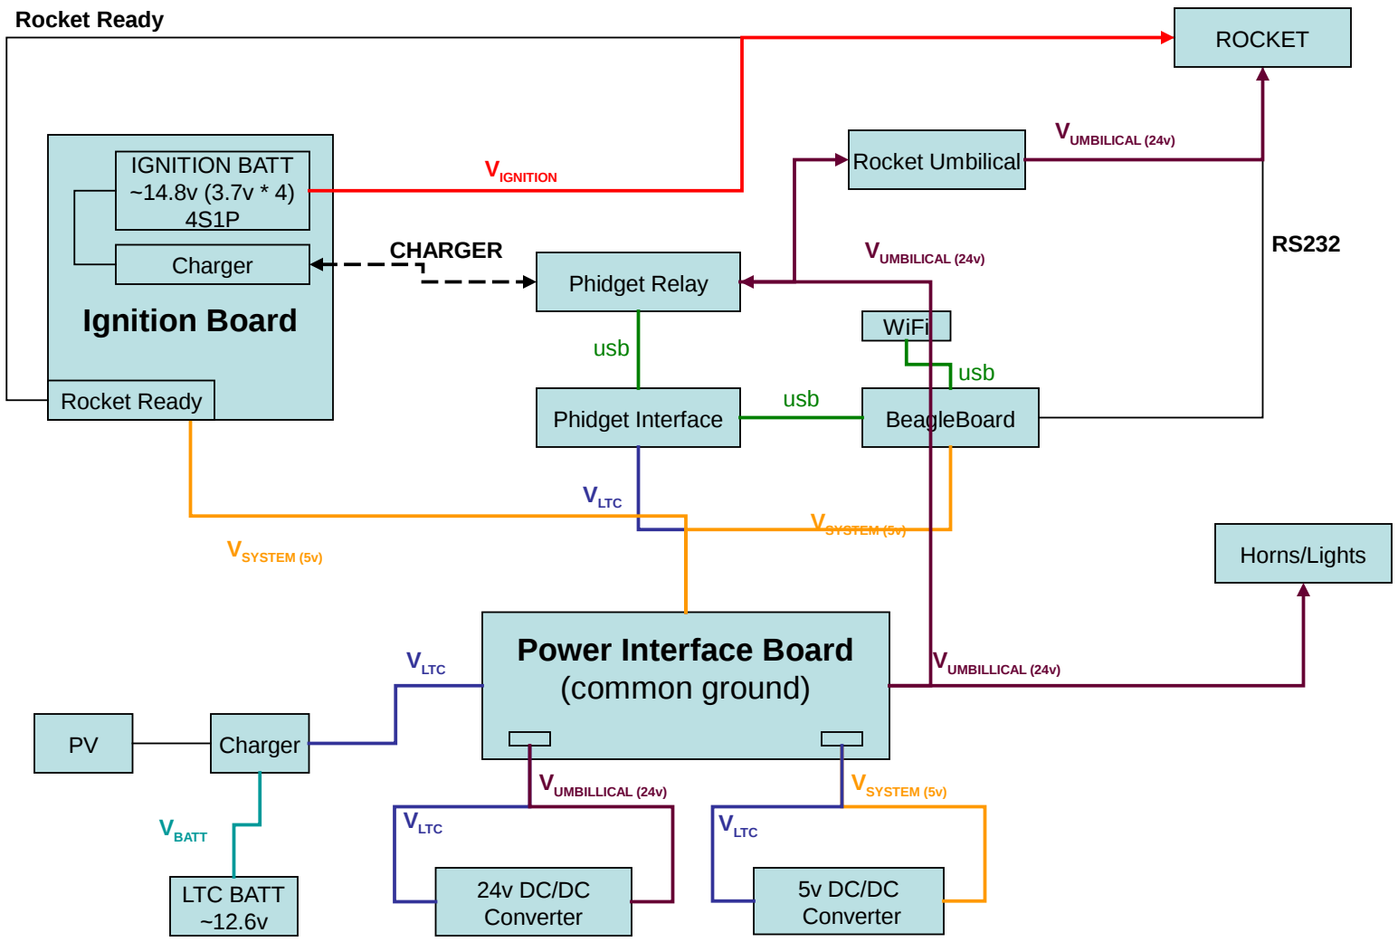
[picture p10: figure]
Power Interface Board (common ground); Charger; LTC BATT ~12.6v; 24v DC/DC Converter; Ignition Board; Phidget Interface; Phidget Relay; BeagleBoard; WiFi; VLTC; VSYSTEM (5v); VBATT; 5v DC/DC Converter; Rocket Umbilical IGNITION BATT ~14.8v (3.7v * 4) 4S1P; Rocket Ready; ROCKET; VIGNITION; usb; VUMBILLICAL (24v); VUMBILICAL (24v); CHARGER; Horns/Lights

## IGNITION PATH & FEATURES

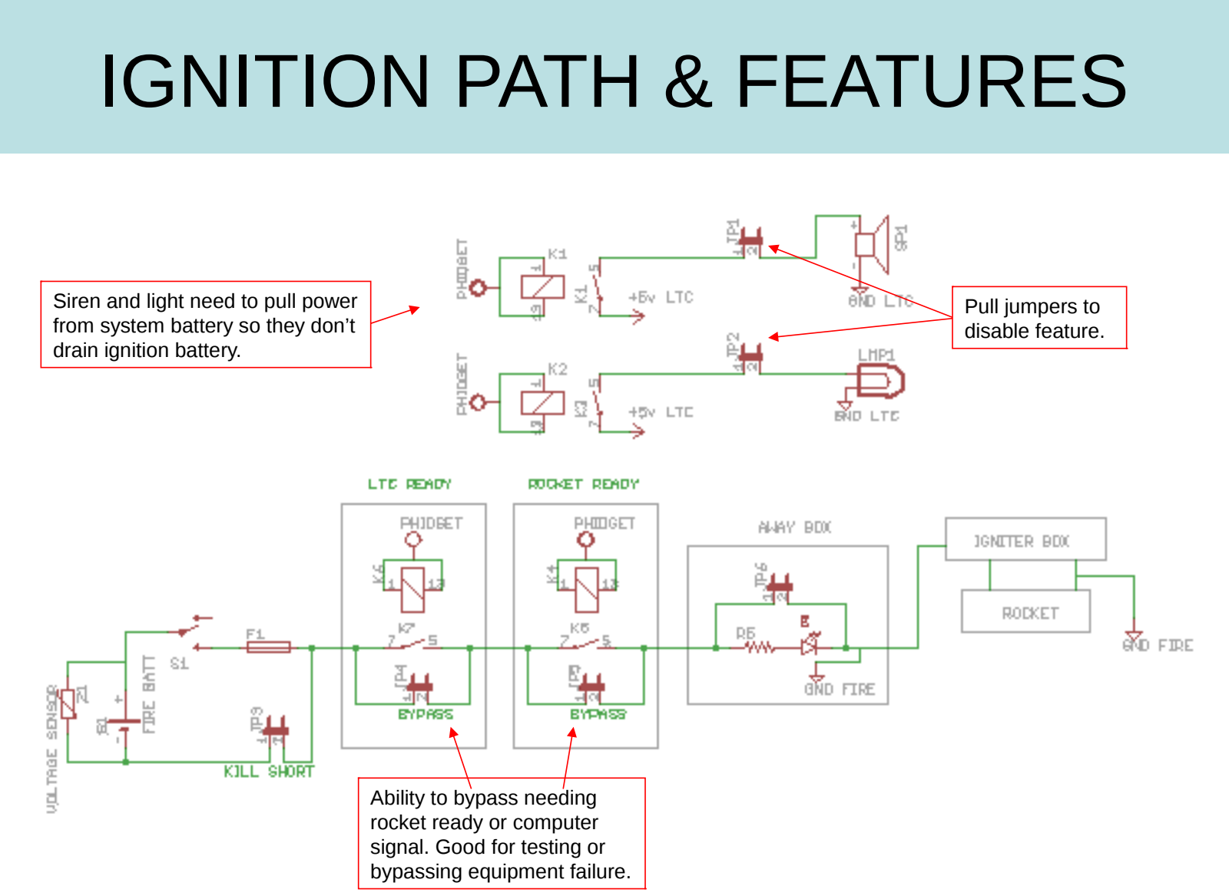
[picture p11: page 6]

Ability to bypass needing
rocket ready or computer
signal. Good for testing or bypassing equipment failure.

Pull jumpers to
disable feature.

Siren and light need to pull power from system battery so they don’t drain ignition battery.

## Power Interface Board

- PROS
– Provide single point to view system health with LED indicators
– Provide on-board conversion of voltage – Provide common ground point
- CONS
– Star topology for power

## Power Interface Board

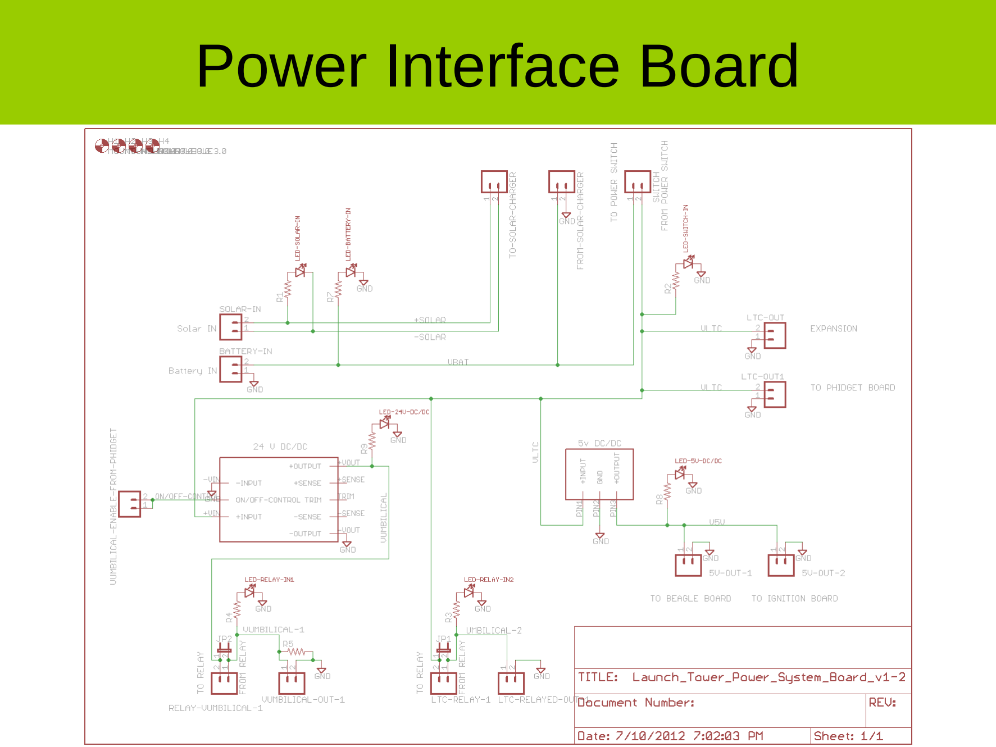
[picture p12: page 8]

## Power Interface Board

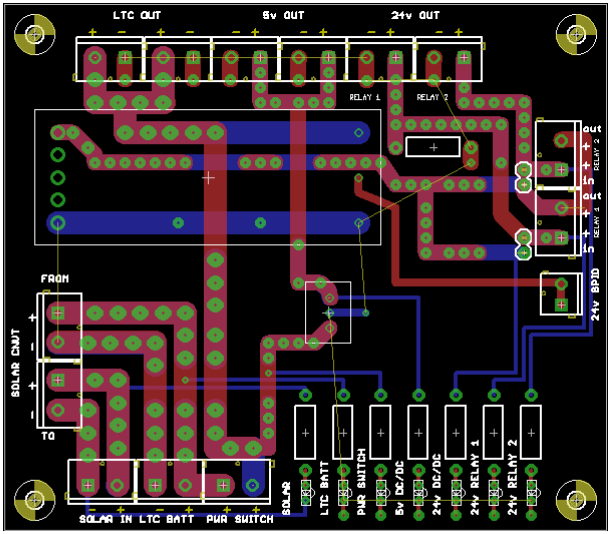
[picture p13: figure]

•Gro

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
of b

o

ard

•Tra

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
are “stitc

h

e

d” to

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
oriz

o

ntally

w/ 9

0

*

h

e

a

d

ers

## Ignition Board

- Combines the capability of rocket-ready with all LIPO battery functions.
- PROS
– LIPO Battery
– Charging functions handled on board and controlled via Phidget relays
– Timing circuit designed for drop-in change of resistor and capacitor
– Has bypass jumpers for testing and bypassing fault on launch day (unsafe)
- CONS
– Not digital (but its cool to go analog sometimes)

## Ignition Board

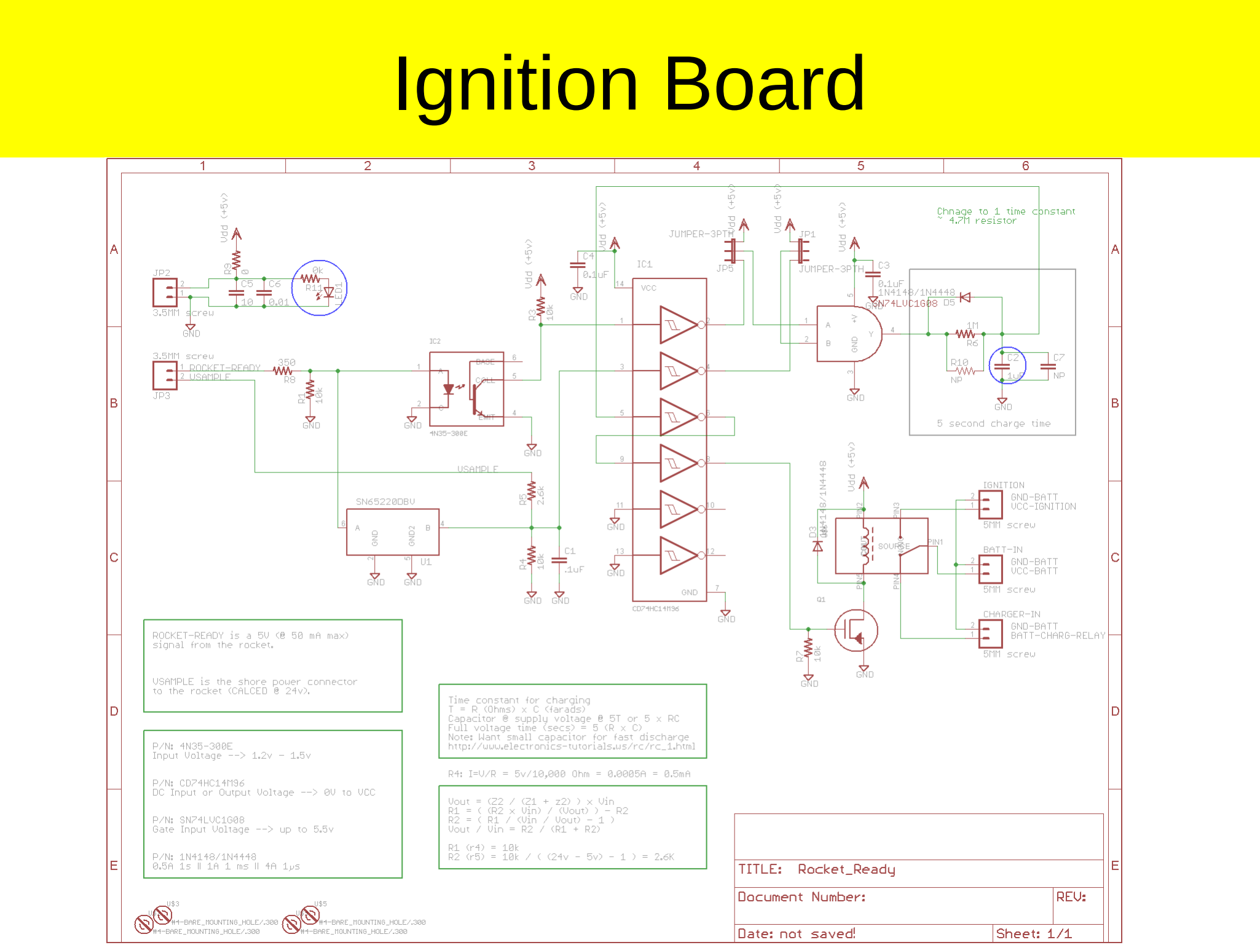
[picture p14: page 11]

## Ignition Board

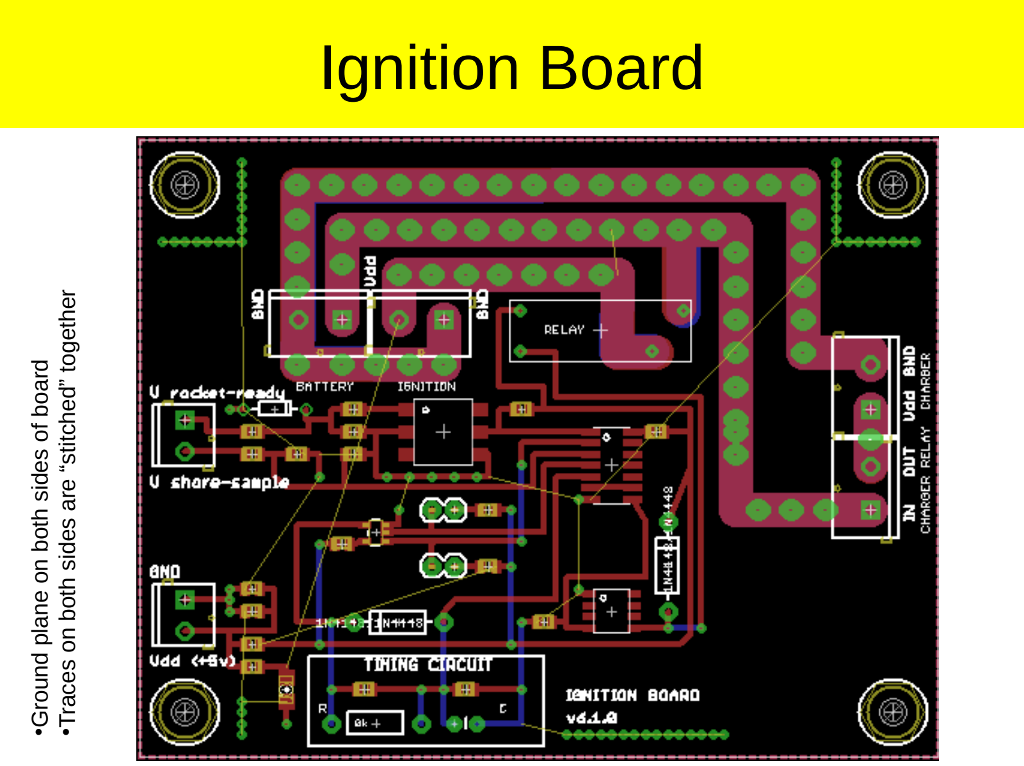
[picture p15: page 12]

•Ground plane on both sides of board

•Traces on both sides are “stitched” together

## Timeline

- Order Parts | 1 week
- Manufacture Boards | 1 week
- Assembly & Test | 2 weeks
– Possible initial rocket access tests
- Mid-August mount to launch tower and mate with rocket for full testing.

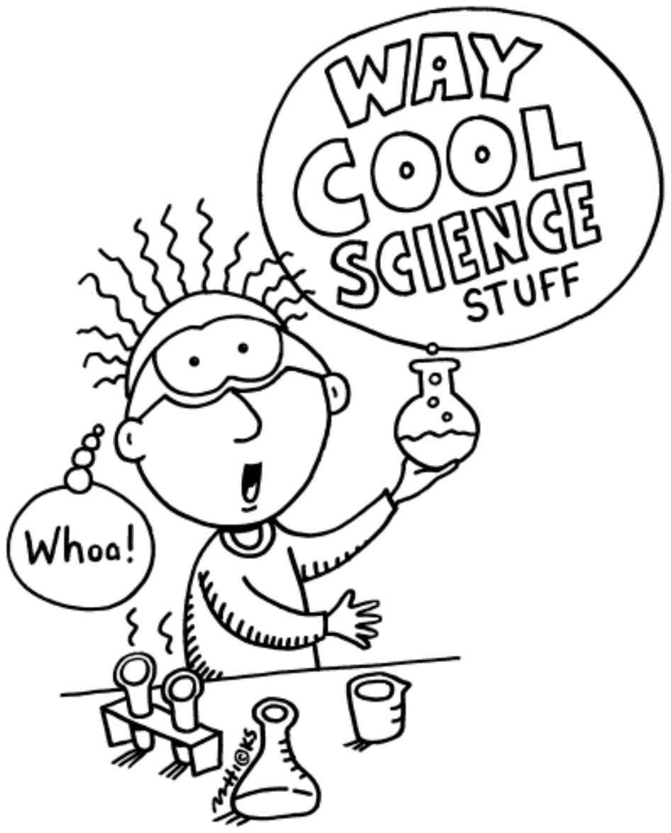
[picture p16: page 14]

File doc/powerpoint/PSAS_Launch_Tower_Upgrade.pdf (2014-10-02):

# PSAS Launch Tower Upgrade System Overview

Created By: Richard Witherspoon Created On: April 19th, 2012

Last Updated By: Richard Witherspoon Last Updated: June 18th, 2012

# Launch Tower Goals

- Create system that can have any Linux computer put as controller.
- I/O management through USB external to control computer.
- Launch via relay interlock from rocket and ground control.
- Disconnect power to rocket
- Manage visual and auditory signaling.
- System should NOT function with loss of computer capabilities. Fail to Safety!
- Control computer physical access if lost through Wi-Fi
- Ample cooling and dust management
- Trigger video acquisition of takeoff.

# TO DO

- FULL PUNCHLIST
- - Ignition Board -
- Select & Purchase the LIPO chargers
- Get dimensions of LIPO batteries
- Adapt Ignition board for LIPO on-board
- Select diodes and LEDs
- - Power Board -
- Add circuitry for umbillical on power board
- Select and purchase 5v and 19v DC/DC converters
- Modify power board for DC/DC converters
- Select diodes and LEDs
- - LTC Box -
- Dimension parts and figure layout in box
- Get dimensions for solar charger
- Figure out exact connections needed
- Figure out how to route wires
- Find a box that meets the dimension requirements
- - BeagleBoard -
- BeagleBoard - make script to launch webservice at boot - instead of manual start
- BeagleBoard - Remove apache
- - Phidgets -
- Application - add error handling and logging
- Get annemometer and wind vane to setup the environmental tacking
- Figure out wire lengths and mountings for sensors on the tower (wind and temp)
- - Other -
- Wiki The setup of everything - in progress

# Block Level Design

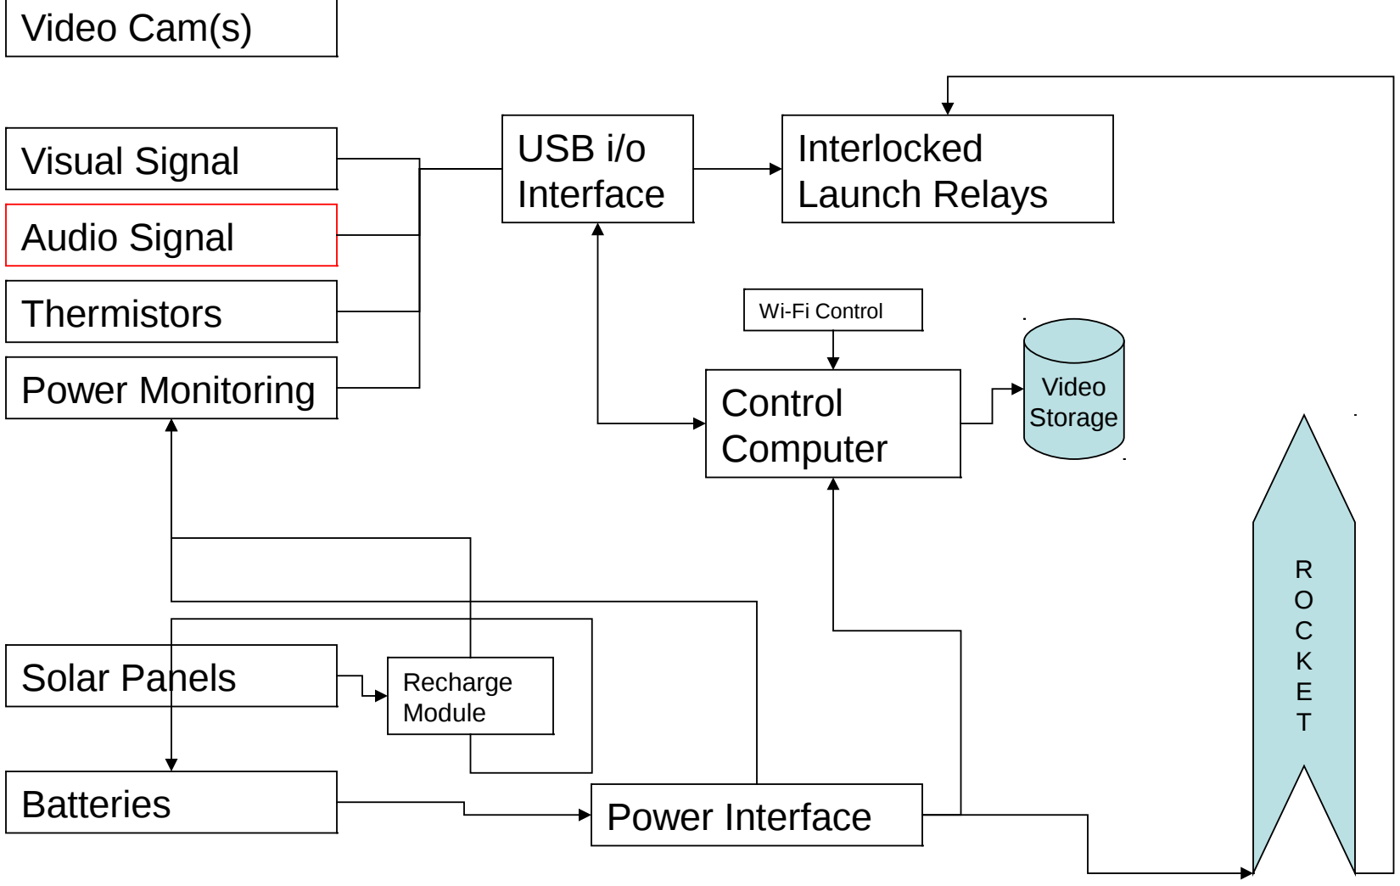
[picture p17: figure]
Batteries; Solar Panels; Video Cam(s); Video Storage; Audio Signal; Visual Signal; Interlocked; Launch Relays; Power Interface; Control Computer; Wi-Fi Control; USB i/o Interface; Thermistors; Power Monitoring; Recharge Module

# Interlocks - CURRENT

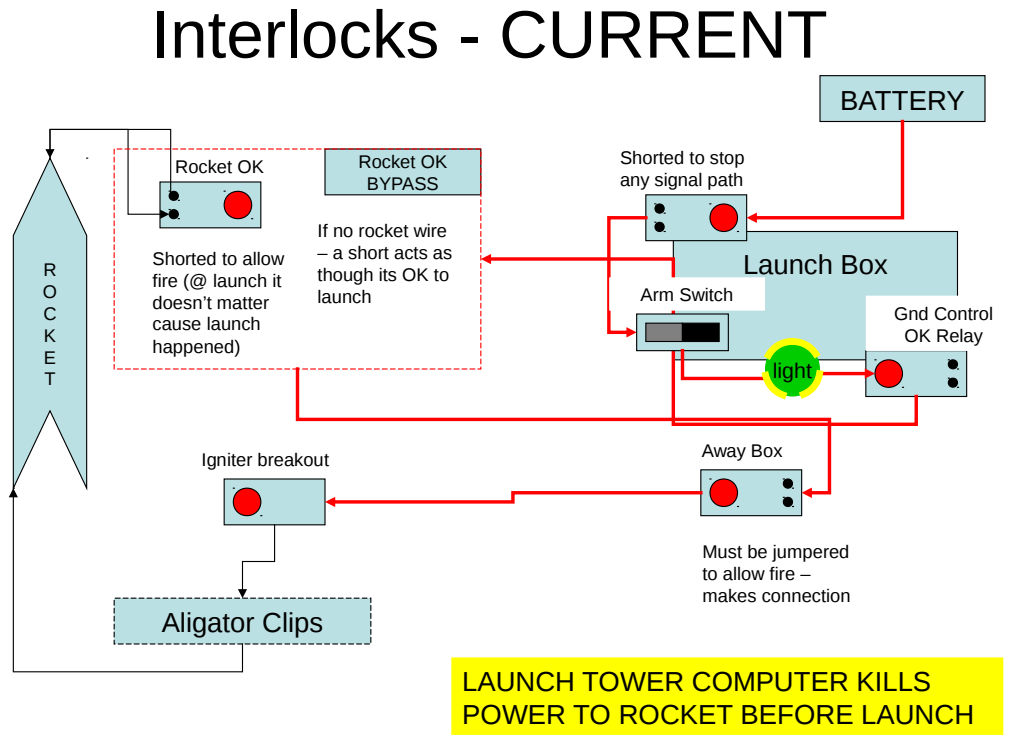
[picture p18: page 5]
Aligator Clips; Launch Box; Igniter breakout; Away Box; Rocket OK BYPASS; BATTERY; Gnd Control OK Relay; Arm Switch; light

Shorted to stop

any signal path Rocket OK

If no rocket wire
– a short acts as
though its OK to
launch

Shorted to allow
fire (@ launch it
doesn’t matter
cause launch
happened)

Must be jumpered
to allow fire –
makes connection

LAUNCH TOWER COMPUTER KILLS
POWER TO ROCKET BEFORE LAUNCH

# Interlocks - NEW

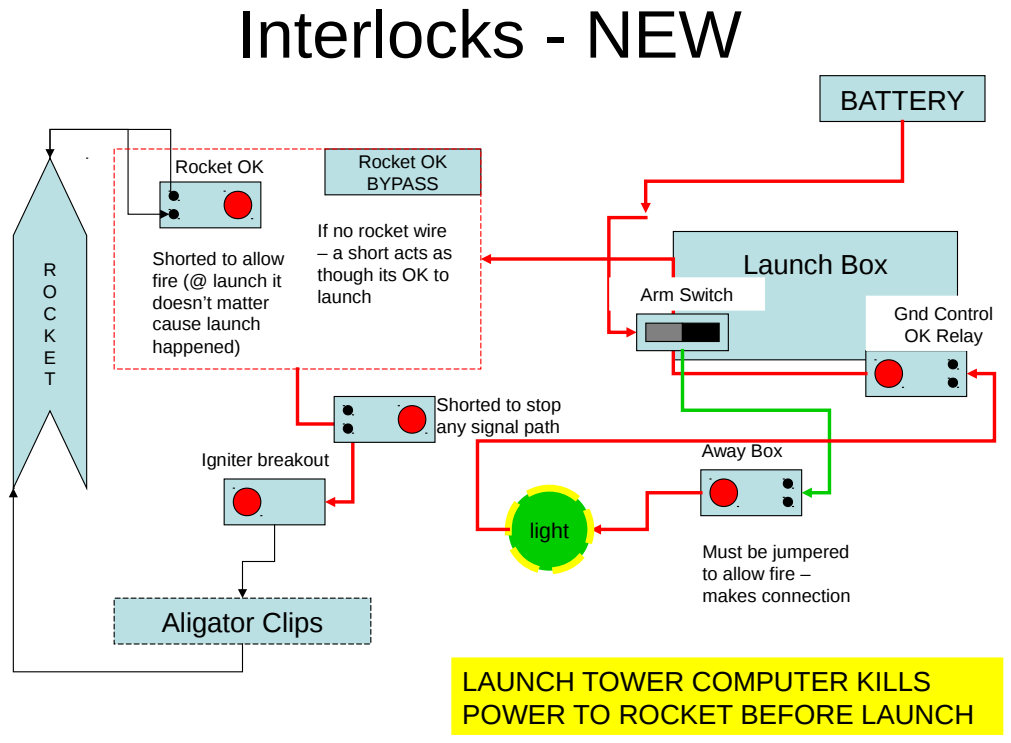
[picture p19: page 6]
Aligator Clips; Launch Box; Igniter breakout; Away Box; Rocket OK; Rocket OK BYPASS; BATTERY; Gnd Control OK Relay; light; Arm Switch

If no rocket wire
– a short acts as
though its OK to
launch

Shorted to allow
fire (@ launch it
doesn’t matter
cause launch
happened)

Shorted to stop
any signal path

Must be jumpered
to allow fire –
makes connection

LAUNCH TOWER COMPUTER KILLS
POWER TO ROCKET BEFORE LAUNCH

# Computer Steps

## - Boots Up - Connects to USB i/o interface - Starts web server and SSH access - Starts launch management software - Starts drivers for webcam access - Login from ground control (via SSH or web access) - View program interface for status and ability to

launch.

# Software Goals

- Take input to begin countdown
- Allow halt/cancel of countdown
- Report on system status
– Batteries
– Solar Cell
– Relays
– Cameras
- Launch sequence
– Start video collection – via GPIO to 3rd-party board (and some form of validation back in)
– Set relays
– Sound horns
– Visual alert
– Send fire signal – This last step must be done again by ground control – NOT automatically in the loop
– Send signal to disconnect shore power to rocket

# Software Structure

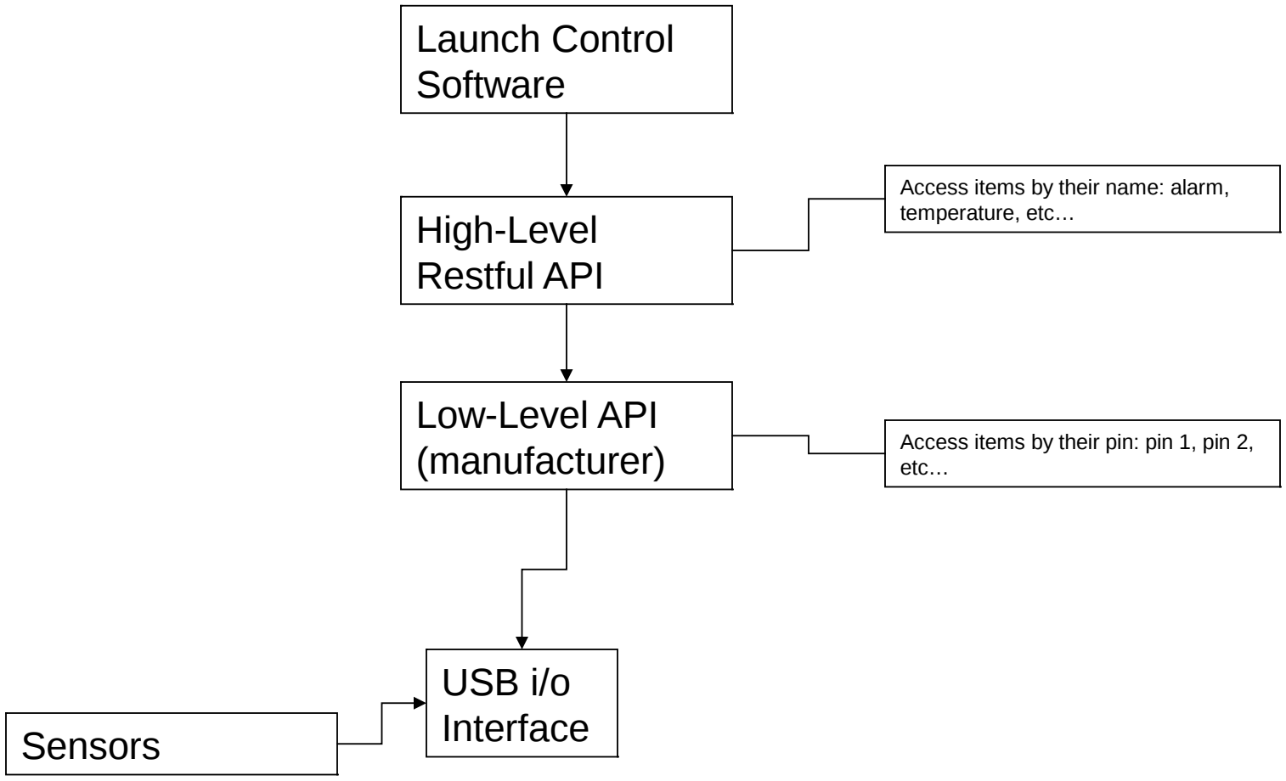
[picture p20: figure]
Low-Level API (manufacturer); USB i/o Interface; High-Level Restful API; Access items by their name: alarm, temperature, etc…; etc…; Sensors; Launch Control Software

Access items by their pin: pin 1, pin 2,

# Timeline

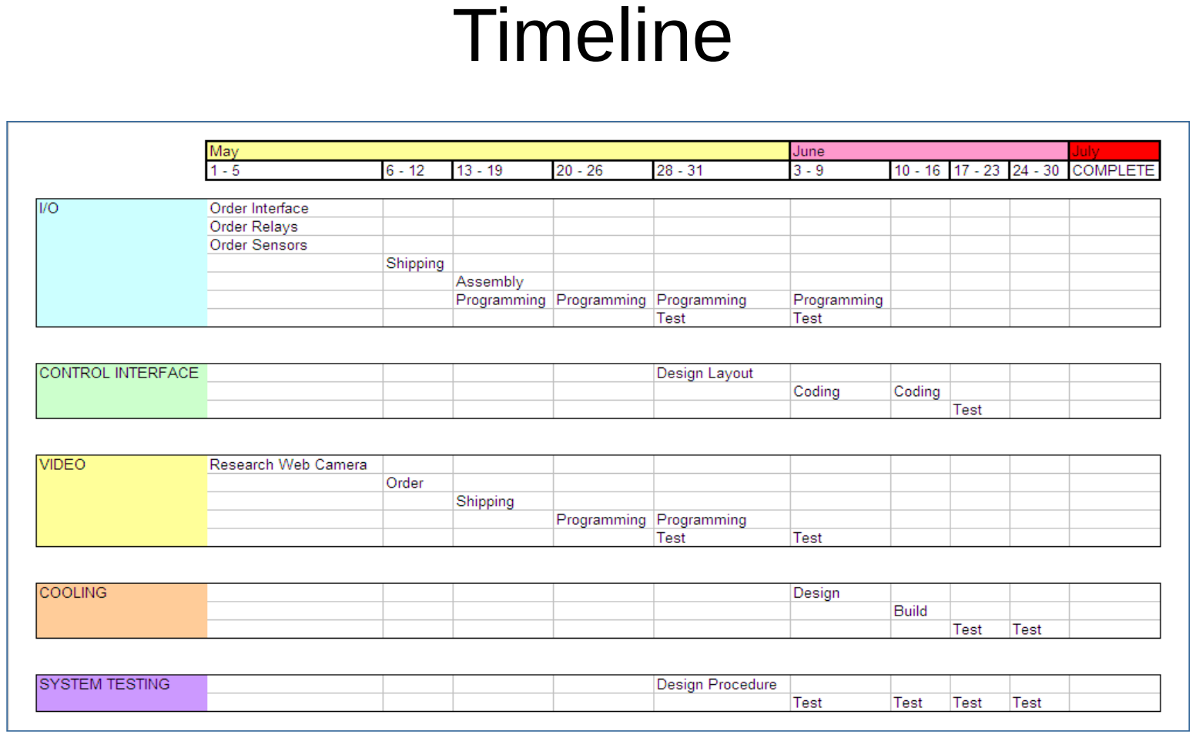
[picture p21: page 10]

# Possible I/O Interfaces

- Phigets
– Website: http://www.phidgets.com/
– Pros
- Lots of libraries in many languages
- Relays, IO, and webcams all with libraries
- Lots of sensors with libraries (immersive heat up to 800*C – in the plume)
- Debian board for integrated development
- Electronics-DIY
– Website: http://electronics-diy.com/USB_IO_Board.php
– Pros
- Super low-cost - $23
- Access control/logging via PHP
- 16 individual microcontroller I/O pins
- 500mA for electronic projects
- Audrino
– Website: http://www.trossenrobotics.com/p/arduino-duemilanove.aspx

# Budget - $500

- USB i/o interface
- Web Cameras
– Under plume
– Wider take-off shot
- Sensors
– Plume Temperature
– Power status
– Thermal Status – Electronics – Thermal Status – Ambient Air
- Siren
- Lights
- Computer system
– NetPC with cooling
– Thermally hardened computer – Ideal Range (30*F - 150*F)
- Cooling
– Some form of cooling for electronics
- Dust mitigation

# Physical Connections

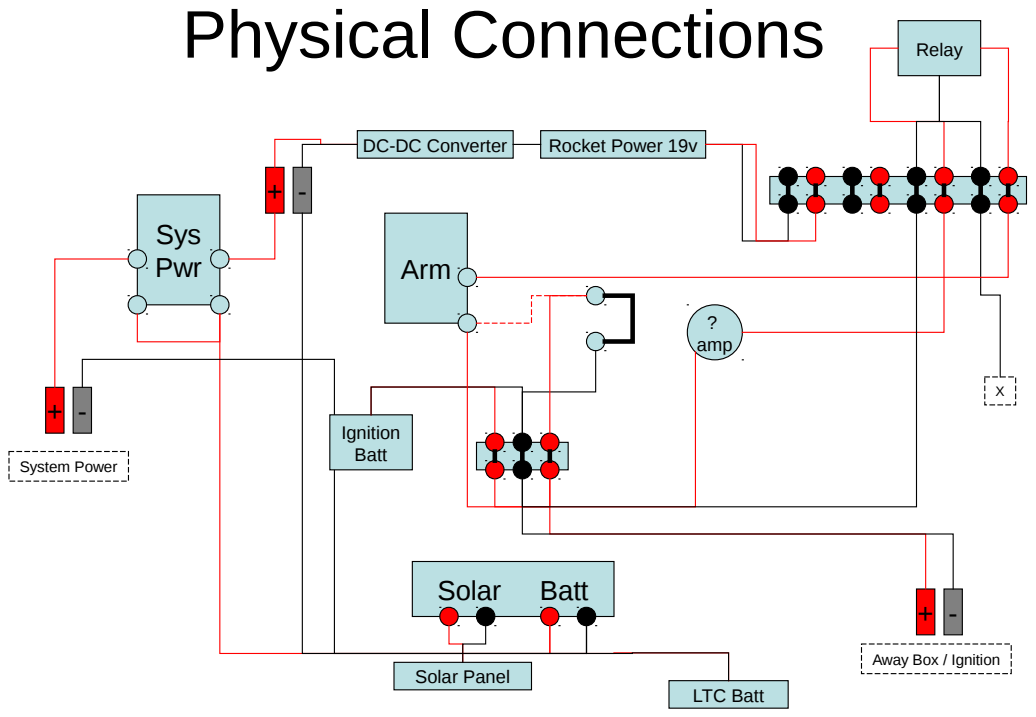
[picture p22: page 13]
Sys Pwr; System Power; Solar; Batt; Solar Panel; LTC Batt; DC-DC Converter; Rocket Power 19v; Arm; Ignition Batt; ? amp; Relay

Away Box / Ignition

# Box Mounting

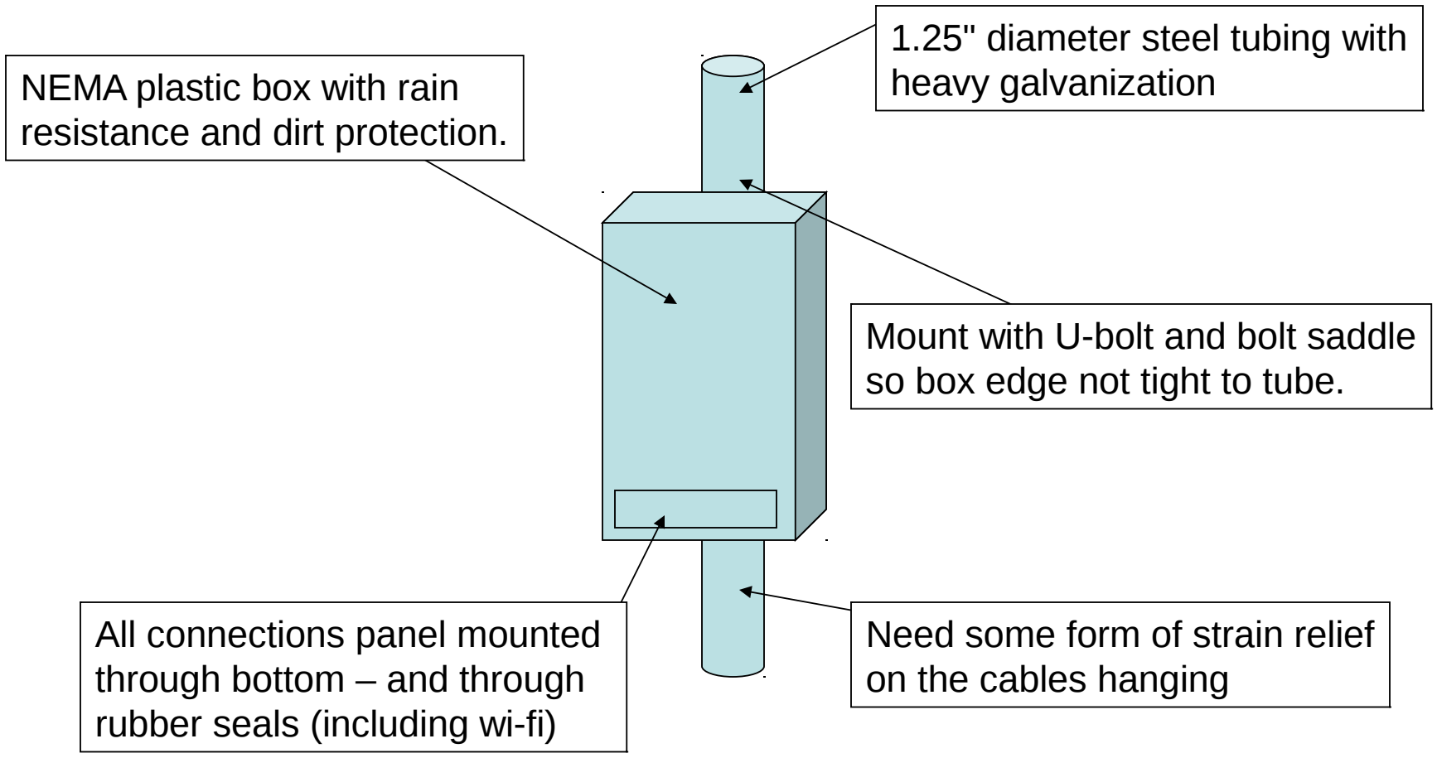
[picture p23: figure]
1.25" diameter steel tubing with heavy galvanization; All connections panel mounted through bottom – and through rubber seals (including wi-fi); Need some form of strain relief on the cables hanging; NEMA plastic box with rain resistance and dirt protection.; Mount with U-bolt and bolt saddle so box edge not tight to tube.

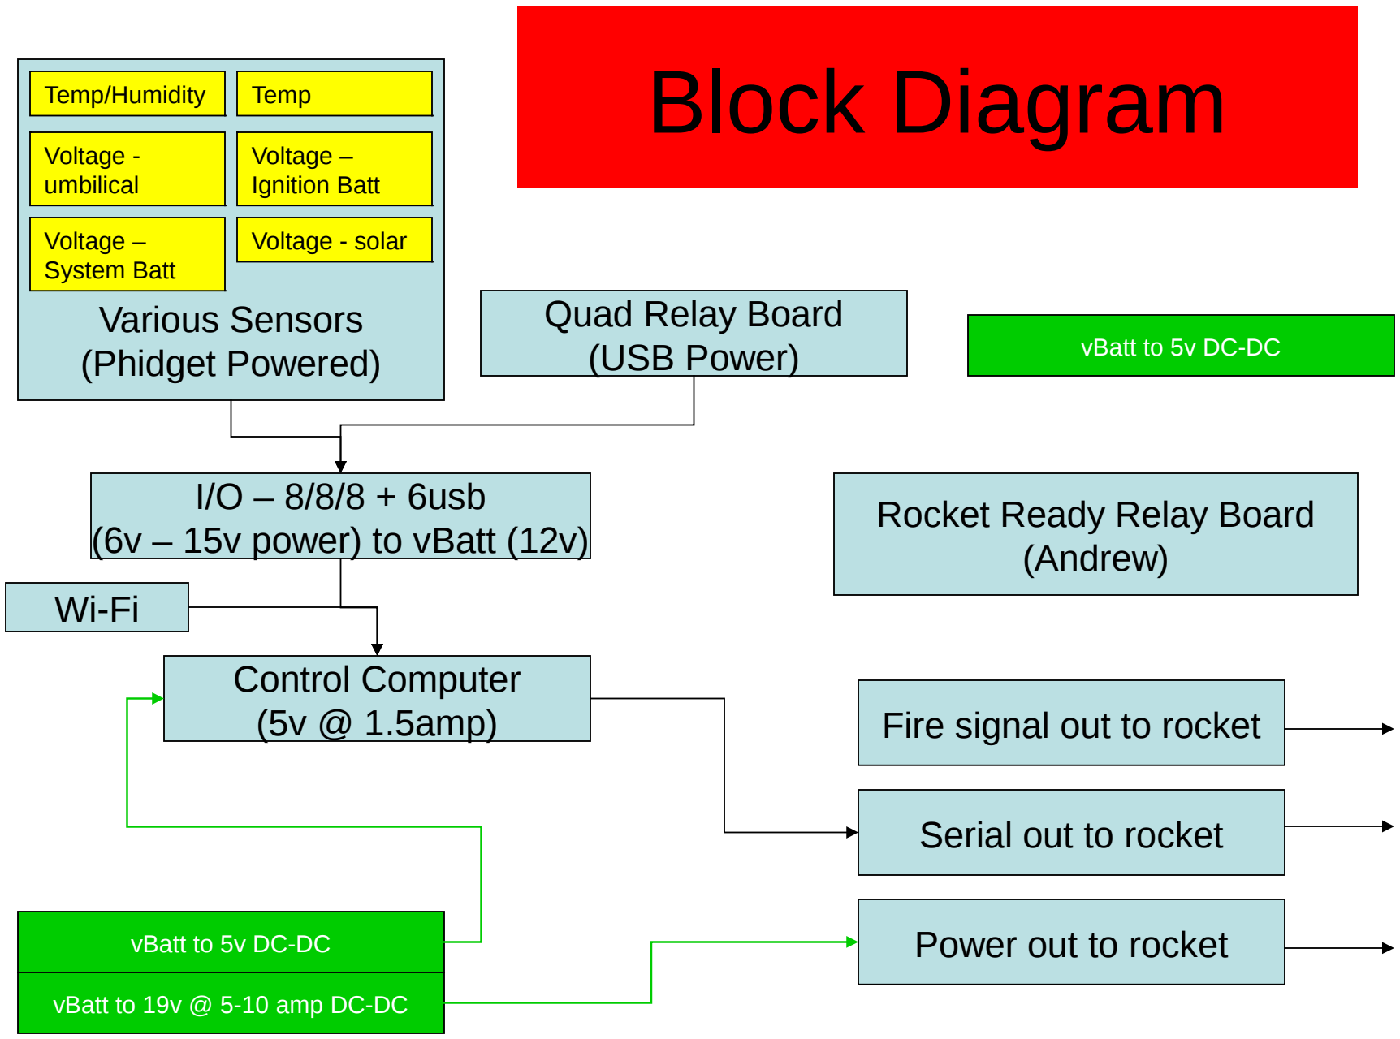
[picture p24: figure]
Block Diagram; Control Computer (5v @ 1.5amp); I/O – 8/8/8 + 6usb; (Andrew); Various Sensors (Phidget Powered); Quad Relay Board (USB Power); Temp/Humidity; Temp; Voltage - umbilical; Voltage - solar; Voltage – Ignition Batt; Voltage – System Batt; Power out to rocket; Serial out to rocket; Fire signal out to rocket; vBatt to 5v DC-DC; vBatt to 19v @ 5-10 amp DC-DC

(6v – 15v power) to vBatt (12v) | Rocket Ready Relay Board

# I/O Design - Phidgets

Control Computer

A – in (1)
A – in (2)
A – in (3)
A – in (4)
A – in (5)
A – in (6)
A – in (7)
A – in (8)

USB – in (1)
USB – in (2)
USB – in (3)
USB – in (4)
USB – in (5)
USB – in (6)

D – out (1)
D – out (2)
D – out (3)
D – out (4)
D – out (5)
D – out (6)
D – out (7)
D – out (8)

I/O – 8/8/8 + 6usb

Temp/Humidity - Ambient

Temp - Electronics

Voltage - Solar
Voltage - Batts
Voltage – Ignition

Wind - Speed

Wind - Direction
Quad Relay

Accelerometer

Web Camera (monitoring)

Voltage – Umbilical

# IGNITION PATH & FEATURES


Ability to bypass needing
rocket ready or computer
signal. Good for testing or bypassing equipment failure.

Pull jumpers to
disable feature.

Siren and light need to pull power from system battery so they don’t drain ignition battery.

# SYSTEM POWER


# Possible Power Interface Card


Puts all power connections onto one monitoring card with LEDs so you can see if
everything is functional right after hook-up.

# Circuit - Phidget


x

DPDT on rocket ready
to Digital i/o

Power System (common ground); Charger; LTC BATT ~12.6v; Charger19v SPS DC/DC Converter; Ignition Board; Phidget Interface; Phidget Relay; BeagleBoard; WiFi; VLTC; SYSTEM (5v); VBATT; Rocket Umbilical; IGNITION BATT ~14.8v (3.7v * 4) 4S1P; Rocket Ready; ROCKET; VIGNITION; usb; Beagleboard; Ignition Board – 5v 100mA (?); VSYSTEM (5v); VUMBILLICAL (24v); VUMBILICAL (24v); CHARGER; Horns/Lights

5v 950mA – no HDMI monitor attached w/ wireless keyboard

Murata OKI-78SR-5/1.5-W36-C

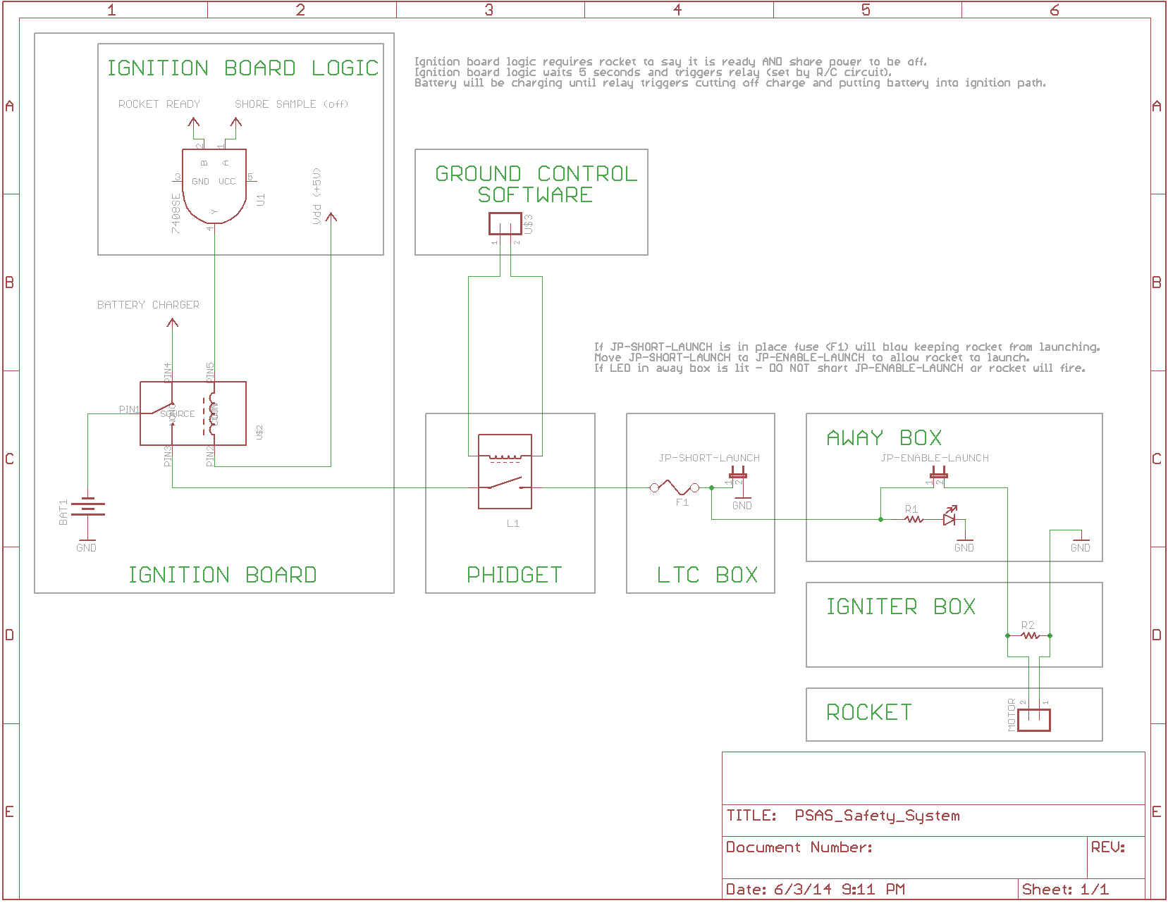
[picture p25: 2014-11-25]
ltc3/doc/ltc2_review/LTC2_Safety_Schematic.png

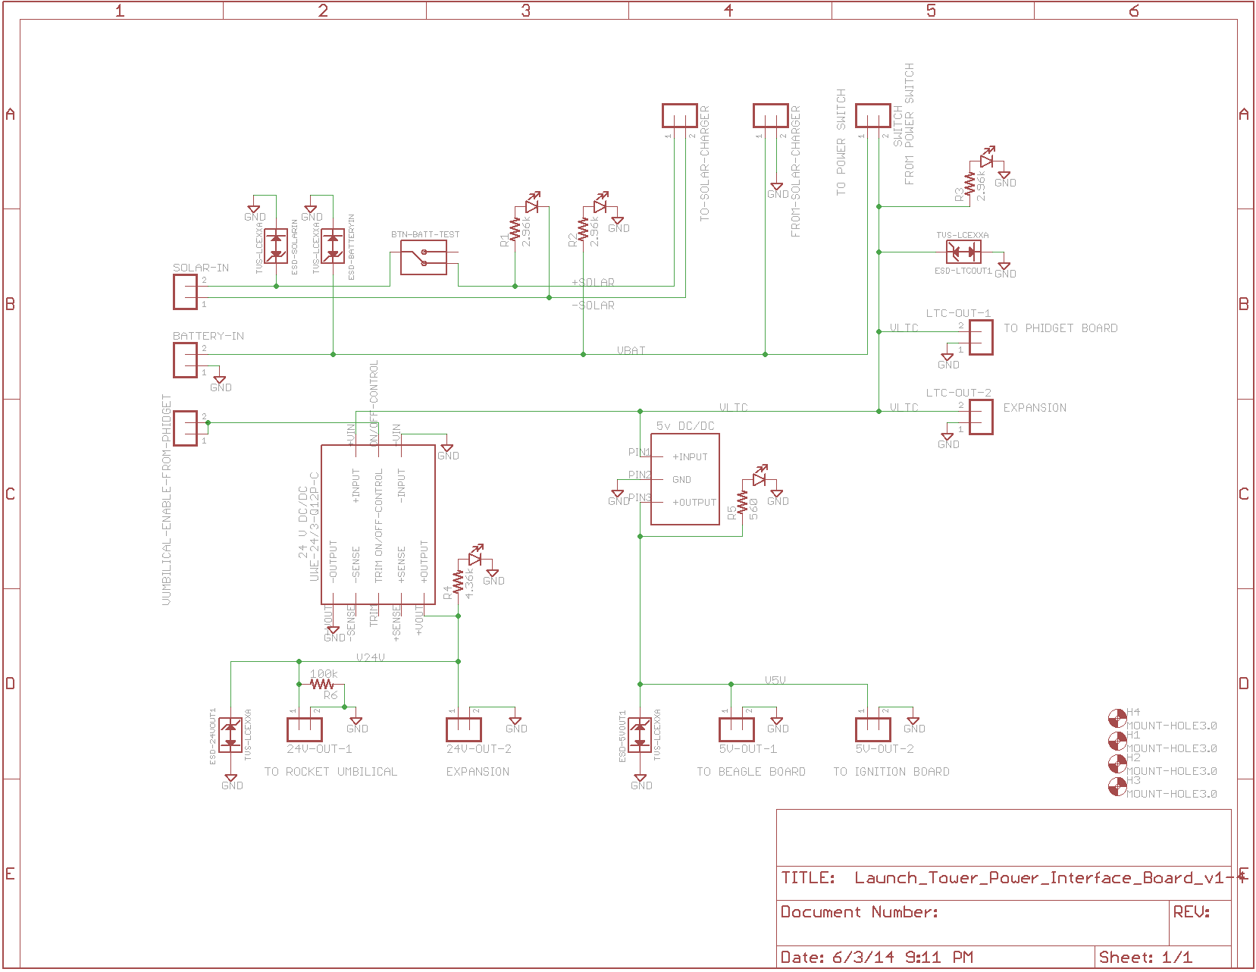
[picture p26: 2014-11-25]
ltc3/doc/ltc2_review/LTC2_Power_Board_Schematic.png

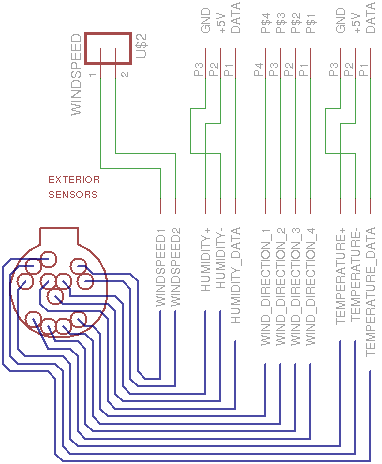
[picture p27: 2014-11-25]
ltc3/doc/ltc2_review/LTC2_Connector_Interface_Schematic.png

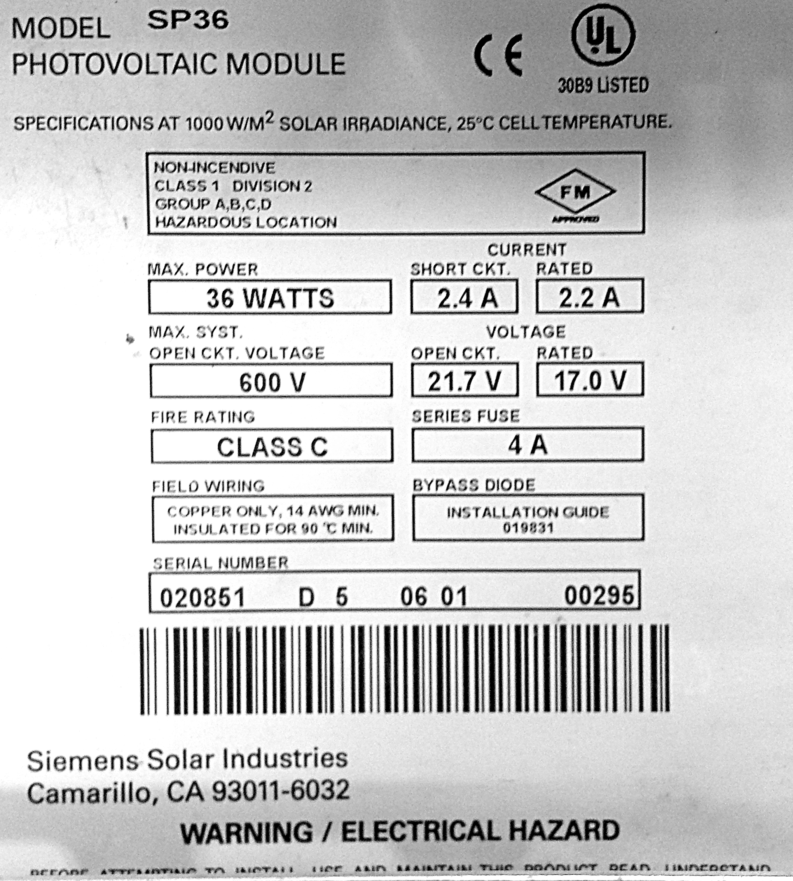
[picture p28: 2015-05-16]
ltc3/doc/design/images/LTC_PV_panel_specs_decal.jpg

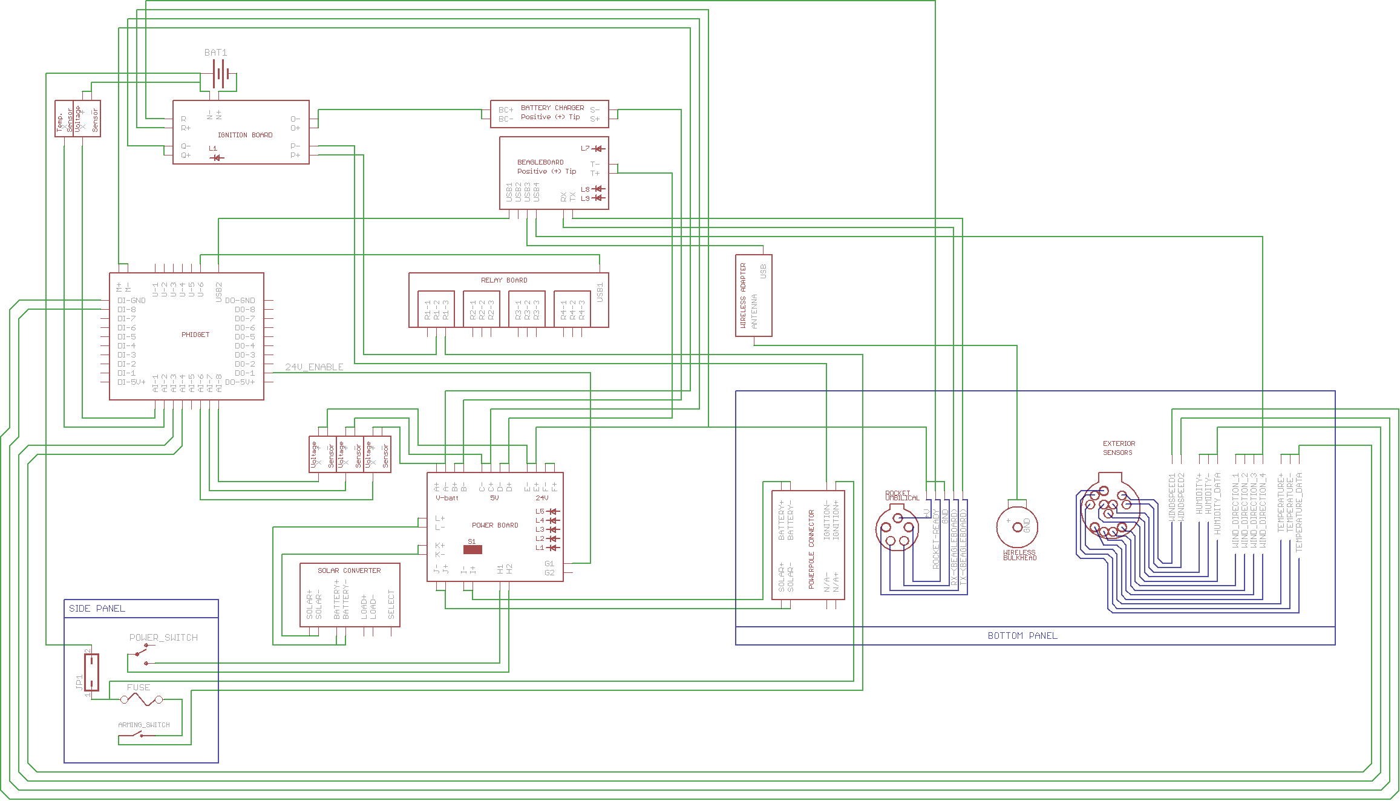
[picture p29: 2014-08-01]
doc/diagrams/LTC_connections_schematic.png

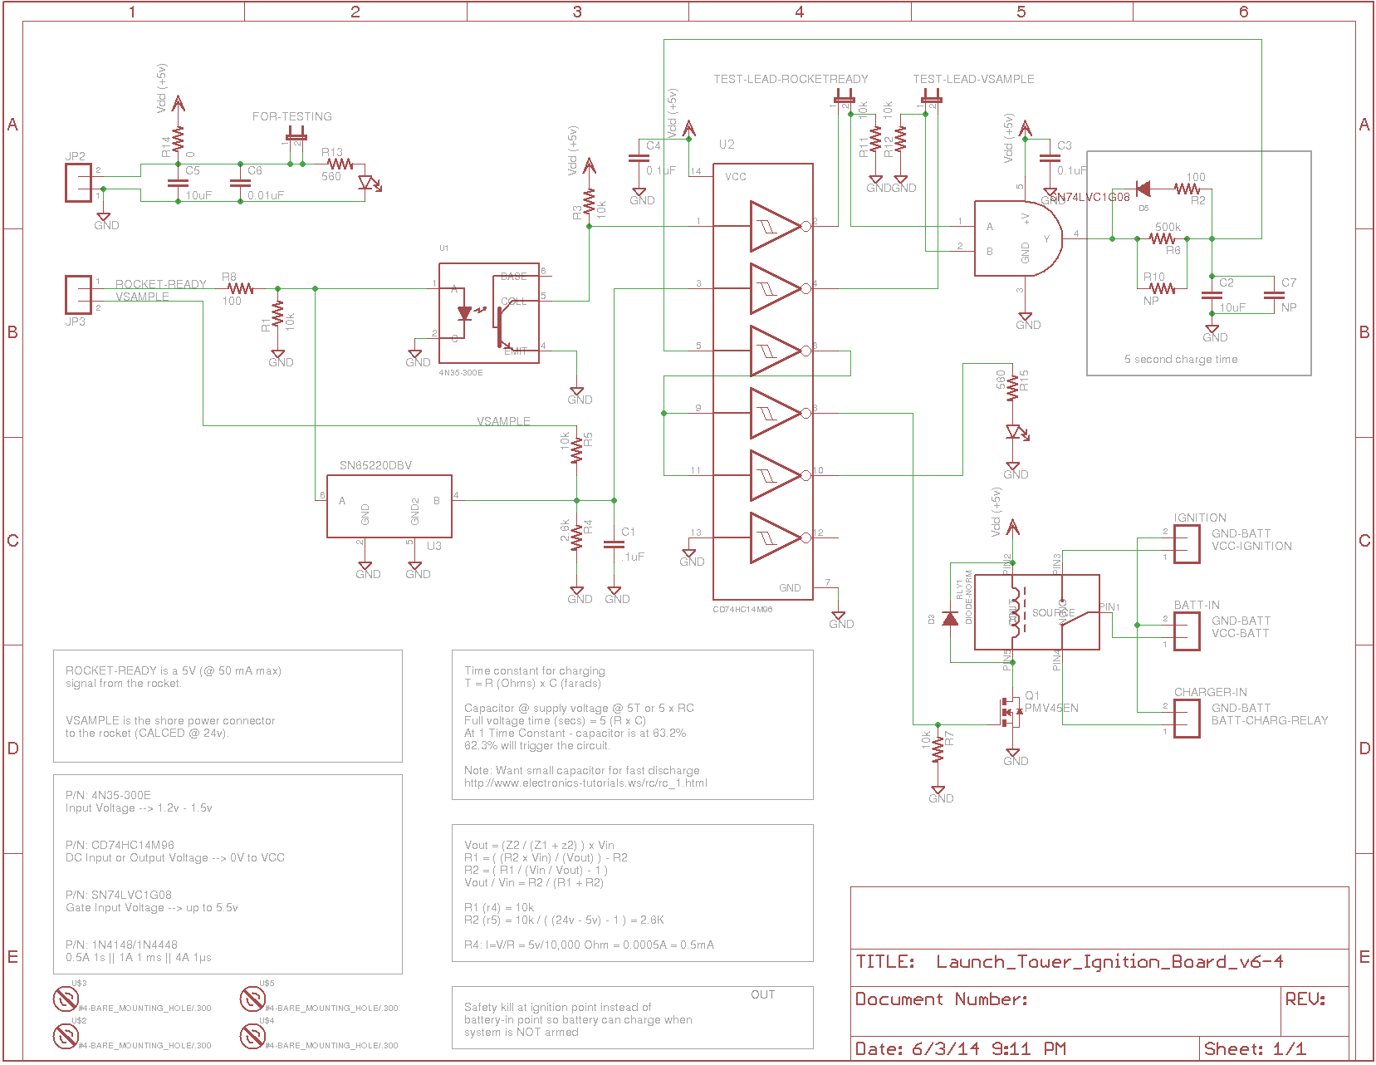
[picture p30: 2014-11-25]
ltc3/doc/ltc2_review/LTC2_Ignition_Board_Schematic.png

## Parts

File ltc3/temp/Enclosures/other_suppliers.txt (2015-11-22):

AutomationDirect
General Purpose NEMA Electrical Enclosures
http://www.automationdirect.com/adc/Overview/Catalog/Enclosures/General_Purpose_Enclosures

Mier Products, Inc.
In-Stock Enclosures, Cabinets, Boxes, or Cans
http://www.mierproducts.com/in-stock_enclosures.html

Bud Industries, Inc.
NEMA Boxes: UL/NEMA/IEC NBA Series
http://www.budind.com/view/NEMA+Boxes/UL_NEMA_IEC+NBA+Series
NEMA Boxes: UL/NEMA/IEC NBE Series
http://www.budind.com/view/NEMA+Boxes/UL_NEMA_IEC+NBE+Series

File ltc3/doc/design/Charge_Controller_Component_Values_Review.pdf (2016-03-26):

# LTC3: Battery Charging Schematic Numbers for LTC3, LT8490

Objective: To review and clarify component value choices for the LT8490 schematic in the LTC3 system for PSAS.

Basic Parameters

Stage 2 Charging Voltage: 33.6V Maximum Charging Current: 10A Maximum Precharge/Trickle Current: 1A Maximum Input Current: 10A Switching Frequency: 202 kHz

Table of Chosen Values

Input Feedback Resistor Network

RFBIN1 | 93.1 kΩ
RFBIN2 | 7.68 kΩ
RDACI1 | 3.32 kΩ
RDACI2 | 16.5 kΩ
CDACI | 33 µF

Output Feedback Resistor Network

RFBOUT1 | 294 kΩ
RFBOUT2 | 10.2 kΩ
RDACO1 | 57.6 kΩ
RDACO2 | 1.5 kΩ
CDACO | .18 µF

Current Limiting

RSENSE1 | 5 mΩ
RSENSE2 | 5 mΩ
RIMON_OUT | 243 kΩ
RIOW | 27.1 kΩ
CIMON_OUT | 10 nF

Input Feedback Resistor Network

The Input Feedback network is essentially what tells the LT8490 the present input voltage and current from the solar panel, and tells the LT8490 the maximum input voltage to accept. The true maximum input voltage is defined as

,

where

We want VX1

to be as close to 6V as possible, which is accomplished by iterating over multiple values of RFBIN1

, RFBIN2

, RDAC1

, and RDAC2

. Given our values, VX1

is 5.971V, giving a percent error of .48% from the ideal value of 6. This means that the LT8490 sees a maximum input voltage of 21.47V.

Due to the nature of the iterative process, some component values were not chosen based on their closest real resistor value, but rather the value that would get VX1 as close to 6V as possible. More information can be found on page 14 of the LT8490 datasheet.

The equation for RFBIN1 can be found on page 14 of the LT8490 datasheet, and is described by

When we set our VMAX

to the short circuit voltage of the solar panel, which is 21.7V, we get a value of 94.7 kΩ for RFBIN1

. The chosen resistor value is 93.1 kΩ.

The equation for RDAC2 can be found on page 14 of the LT8490 datasheet, and is described by

Given our RFBIN1 value of 94.7 kΩ and our VMAX of 21.7V, we get a RDACI2 value of 16.59 kΩ. The chosen resistor value is 16.5 kΩ.

The equation for RFBIN2 can be found on page 14 of the LT8490 datasheet, and is described by

Given our RFBIN1 value of 94.7 kΩ and our RDACI2 value of 16.59 kΩ, our resulting RFBIN2 value is 7.808kΩ. The chosen RFBIN2 value is 7.68 kΩ.

The equation for RDACI1 can be found on page 14 of the LT8490 datasheet, and is described by

Given our RDACI2 value of 16.59 kΩ, the resulting RDACI1 value is 3.318 kΩ. The chosen RDACI1 value is 3.32 kΩ.

The equation for CDACI can be found on page 14 of the datasheet and is described by

Given our RDACI1 value of 3.318 kΩ, we get a CDACI value of .301 µF. The chosen CDACI value is .33 µF.

Output Feedback Resistor Network

The Output Feedback Resistor Network determines the maximum output voltage of the LT8490, which determines stage 3 charging voltage of the LiPo cells. The accuracy of this network is critical to fully charging the batteries. The true stage 3 voltage is described by

,
where

We want VX3

to be as close as possible to 33.6 V. With our chosen resistor values, our stage 3 voltage is 33.225 V. This is a 1.04% error from the ideal value of 33.6 V. These values were chosen by iterating over multiple real resistor values.

Due to the nature of the iterative process, some component values were not chosen based on their closest real resistor value, but rather the value that would get VX3 as close to 33.6 V as possible. This process is described on page 17 of the LT8490 datasheet.

The equation for RFBOUT1 can be found on page 17 of the LT8490 datasheet, and is described by

RFBOUT2

is a chosen resistor value, with recommended values 4.99 kΩ and 49.9 kΩ. Our chosen RFBOUT2 value is 10.2 kΩ. Given our chosen RFBOUT2 value of 10.2 kΩ and our stage 2 voltage limit of 33.6 V (VS2

), our calculated RFBOUT1

is 291.12 kΩ. The chosen RFBOUT1 value is 294 kΩ.

The equation for RDACO2 can be found on page 17 of the LT8490 datahseet, and is described by

Given our RFBOUT1 value of 291.12 kΩ, our RFBOUT2 value of 10.2 kΩ, and our VS2 of 33.6 V, the resulting RDACO2 value is 53.14 kΩ. The chosen RDACO2 value is 57.6 kΩ.

The equation for RDACO1 can be found on page 17 of the LT8490 datahseet, and is described by

Given our RDACO2 value of 53.14 kΩ, we get an RDACO1 value of 10.68 kΩ. The chosen value of

RDACO1

is 11.5 kΩ.

The equation for CDACO can be found on page 17 of the LT8490 datasheet, and is described by

Given our RDACO1 value of 10.68 kΩ, the resulting CDACO value is .174 µF. The chosen value of

CDACO

is .18 µF.

Input Current Limiting

Because our design incorporates a DC Lab Supply power input option, input current limiting is necessary. Current limiting is accomplished by adjusting the value of RSENSE1 which measures the input current from either the lab supply or the solar panel. The voltage across RSENSE1 affects the voltage on the IMON_IN pin, dropping the VC voltage, and thus reducing the input current. More information can be found on page 19 of the LT8490 datasheet.

The equation to determine RSENSE1 can be found on page 19 of the LT8490 datasheet and is described by

Given our desired I

IN(MAX) of 10 A, the resulting RSENSE1 value is 5.05 mΩ. The chosen RSENSE1 value is 5 mΩ.

Charge Current Limiting

The maximum charging current is configured by a network dependent on RSENSE2

. The current
passing through RSENSE2

is measured and a voltage drop across IMON_OUT is created. When the IMON_OUT voltage is above 1.208 V, VC

is reduced, and thus the charging current is limited. More information can be found on page 18 of the LT8490 datasheet.

The equation to determine RSENSE2 can be found on page 19 of the LT8490 datasheet and is described by

Given our IOUT(MAX) of 10 A, the resulting RSENSE2 value is 4.97 mΩ. The chosen value for RSENSE2 is 5 mΩ.

The equation to determine RIMON_OUT can be found on page 19 of the LT8490 datasheet, and is described by

Given our value of 4.97 mΩ for RSENSE2 and 1 A for IOUT(MAXSO)

(precharge current maximum), the resulting value for RIMON_OUT

is 241.6 kΩ. The chosen value is 243 kΩ.

The equation for RIOW can be found on page 19 of the LT8490 datasheet, and is described by

Given our RIMON_OUT value of 241.6 kΩ, the resulting RIOW value is 27.01 kΩ. The chosen RIOW value is 27.1 kΩ.

The values for RIOR and CIMON_OUT are given as 3.01 kΩ and 10 nF are given in the LT8490 datasheet on page 19.

Temperature Sensing

Temperature sensing is accomplished using the TEMPSENSE pin on the LT8490. With the AVDD pin, a voltage divider is created between an 11.5 kΩ resistor and a 10 kΩ, ß = 3380 NTC thermistor. The voltage on the TEMPSENSE pin then tells the LT8490 the battery temperature.

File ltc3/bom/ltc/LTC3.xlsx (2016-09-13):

Refs | value | Spec | Note | Mfg_Name | Mfg_PN | Mfg_Description | datasheet | footprint
C201 | 1μ | 75V | - | TDK | CGA4J3X7S2A105K125AB | 100V X7S 10% | ~ | Capacitors_SMD:C_0805
C202 | 2.2μ | 75V X7R | - | Murata | GRM32ER72A225KA35L | 100V X7R 10% | ~ | Capacitors_SMD:C_1210
C203 | 470μ | 75V | - | Nichicon | UVZ2A471MHD | 100V 20% | ~ | Capacitors_ThroughHole:C_Radial_D16_L25_P7.5
C204 | 1μ | 75V | - | TDK | CGA4J3X7S2A105K125AB | 100V X7S 10% | ~ | Capacitors_SMD:C_0805
C205 | 0.1μ | 10V | - | Murata | GCM21BR72A104KA37L | 100V X7R 10% | ~ | Capacitors_SMD:C_0805
C206 | 4.7μ | 75V X7R | - | Murata | GRM219R72A472KA01D | 100V X7R 10% | ~ | Capacitors_SMD:C_0805
C207 | 4.7μ | 75V X7R | - | Murata | GRM219R72A472KA01D | 100V X7R 10% | ~ | Capacitors_SMD:C_0805
C208 | 4.7μ | 75V X7R | - | Murata | GRM219R72A472KA01D | 100V X7R 10% | ~ | Capacitors_SMD:C_0805
C209 | 4.7μ | 75V X7R | - | Murata | GRM219R72A472KA01D | 100V X7R 10% | ~ | Capacitors_SMD:C_0805
C210 | 470μ | 75V | - | Nichicon | UVZ2A471MHD | 100V 20% | ~ | Capacitors_ThroughHole:C_Radial_D16_L25_P7.5
C211 | 1μ | 75V | - | TDK | CGA4J3X7S2A105K125AB | 100V X7S 10% | ~ | Capacitors_SMD:C_0805
C212 | 4.7μ | 75V X7R | - | Murata | GRM219R72A472KA01D | 100V X7R 10% | ~ | Capacitors_SMD:C_0805
C213 | 4.7μ | 75V X7R | - | Murata | GRM219R72A472KA01D | 100V X7R 10% | ~ | Capacitors_SMD:C_0805
C214 | 4.7μ | 75V X7R | - | Murata | GRM219R72A472KA01D | 100V X7R 10% | ~ | Capacitors_SMD:C_0805
C215 | 4.7μ | 75V X7R | - | Murata | GRM219R72A472KA01D | 100V X7R 10% | ~ | Capacitors_SMD:C_0805
C216 | 470μ | 75V | - | Nichicon | UVZ2A471MHD | 100V 20% | ~ | Capacitors_ThroughHole:C_Radial_D16_L25_P7.5
C217 | 1μ | 75V | - | TDK | CGA4J3X7S2A105K125AB | 100V X7S 10% | ~ | Capacitors_SMD:C_0805
C301 | 0.1μ | 5V | - | Murata | GCM21BR72A104KA37L | 100V X7R 10% | ~ | Capacitors_SMD:C_0805
C401 | 10μ | 10V | - | Murata | GRM21BR71A106KE51L | 10V X7R 10% | ~ | Capacitors_SMD:C_0805
C402 | NP | 10V | - | - | - | - | ~ | Capacitors_SMD:C_1206
C403 | 0.1μ | 50V | - | Murata | GCM21BR72A104KA37L | 100V X7R 10% | ~ | Capacitors_SMD:C_0805
C404 | 1μ | - | - | TDK | CGA4J3X7S2A105K125AB | 100V X7S 10% | ~ | Capacitors_SMD:C_0805
C405 | 0.1μ | - | - | Murata | GCM21BR72A104KA37L | 100V X7R 10% | ~ | Capacitors_SMD:C_0805
C406 | 0.1μ | - | - | Murata | GCM21BR72A104KA37L | 100V X7R 10% | ~ | Capacitors_SMD:C_0805
C501 | 1μ | 25V | - | TDK | CGA4J3X7S2A105K125AB | 100V X7S 10% | ~ | Capacitors_SMD:C_0805
C502 | 1μ | 25V | - | TDK | CGA4J3X7S2A105K125AB | 100V X7S 10% | ~ | Capacitors_SMD:C_0805
C503 | 1μ | 25V | - | TDK | CGA4J3X7S2A105K125AB | 100V X7S 10% | ~ | Capacitors_SMD:C_0805
C504 | 1μ | 25V | - | TDK | CGA4J3X7S2A105K125AB | 100V X7S 10% | ~ | Capacitors_SMD:C_0805
D201 | CDSU4148 | - | - | Comchip | CDSU4148 | Standard 75V 150mA | https://github.com/psas/launch-tower/blob/master/ltc3/doc/datasheets/semiconductors/ComChip-CDSU4148-SMD_Switching_Diode.pdf | Diodes_SMD:SOD-523
D202 | CDSU4148 | - | - | Comchip | CDSU4148 | Standard 75V 150mA | https://github.com/psas/launch-tower/blob/master/ltc3/doc/datasheets/semiconductors/ComChip-CDSU4148-SMD_Switching_Diode.pdf | Diodes_SMD:SOD-523
D203 | CDSU4148 | - | - | Comchip | CDSU4148 | Standard 75V 150mA | https://github.com/psas/launch-tower/blob/master/ltc3/doc/datasheets/semiconductors/ComChip-CDSU4148-SMD_Switching_Diode.pdf | Diodes_SMD:SOD-523
D401 | CDSU4148 | - | - | Comchip | CDSU4148 | Standard 75V 150mA | https://github.com/psas/launch-tower/blob/master/ltc3/doc/datasheets/semiconductors/ComChip-CDSU4148-SMD_Switching_Diode.pdf | Diodes_SMD:SOD-523
D402 | CDSU4148 | - | - | Comchip | CDSU4148 | Standard 75V 150mA | https://github.com/psas/launch-tower/blob/master/ltc3/doc/datasheets/semiconductors/ComChip-CDSU4148-SMD_Switching_Diode.pdf | Diodes_SMD:SOD-523
D403 | RED | - | Ready-To-Launch | Lite-On | LTST-C150CKT |  | https://github.com/psas/launch-tower/blob/master/ltc3/doc/datasheets/indicators/Lite_On-LTST_C150CKT-LED_Red_1206.pdf | LEDs:LED_1206
D404 | CDSU4148 | - | - | Comchip | CDSU4148 | Standard 75V 150mA | https://github.com/psas/launch-tower/blob/master/ltc3/doc/datasheets/semiconductors/ComChip-CDSU4148-SMD_Switching_Diode.pdf | Diodes_SMD:SOD-523
D405 | RED | - | Rocket_Ignite | Lite-On | LTST-C150CKT |  | https://github.com/psas/launch-tower/blob/master/ltc3/doc/datasheets/indicators/Lite_On-LTST_C150CKT-LED_Red_1206.pdf | LEDs:LED_1206
D406 | 3.3V | - | - | ON Semi | MM3Z3V3T1G | Zener 3.3V 300mW ±6% | https://github.com/psas/launch-tower/blob/master/ltc3/doc/datasheets/semiconductors/ON_Semi-MM3ZxxxT1G_Series-Zener_Voltage_Regulators.pdf | Diodes_SMD:SOD-323
D407 | Yellow, Lg. | - | OFF-BOARD, Batt. Relay Closed | Dialight | 557-1702-203F | Yellow 5V 80mA 17.8mm | https://github.com/psas/launch-tower/blob/master/ltc3/doc/datasheets/indicators/Dialight-557_Series-High_Intensity_LED_Panel_Mount_Indicators.pdf | ~
D408 | Yellow, Lg. | - | OFF-BOARD, Ign. Relay Closed | Dialight | 557-1702-203F | Yellow 5V 80mA 17.8mm | https://github.com/psas/launch-tower/blob/master/ltc3/doc/datasheets/indicators/Dialight-557_Series-High_Intensity_LED_Panel_Mount_Indicators.pdf | ~
D409 | Red, Lg. | - | OFF-BOARD, Ignition HOT | Dialight | 557-1502-203F | Red 5V 80mA 17.8mm | https://github.com/psas/launch-tower/blob/master/ltc3/doc/datasheets/indicators/Dialight-557_Series-High_Intensity_LED_Panel_Mount_Indicators.pdf | ~
J401 | RJ45 | - | - | Stewart | SS-7188S-A-NF | Right angle, Shielded Cat5e | https://github.com/psas/launch-tower/blob/master/ltc3/doc/datasheets/connectors/Stewart-SS7188S-RJ45_Shielded_Jack.pdf | LTC3:RJ45_8_SHIELDED
JP301 | Pin Head 1x2 | - | WR_ENABLE | - | - | - | ~ | Pin_Headers:Pin_Header_Straight_1x02
JP401 | Banana Jack 1x2 | - | Shorting Bar | - | - | - | ~ | ~
JP601 | Pin Head 1x3 | - | Trigger Level | - | - | - | ~ | Pin_Headers:Pin_Header_Straight_1x03
JP602 | Pin Head 1x3 | - | Trigger Level | - | - | - | ~ | Pin_Headers:Pin_Header_Straight_1x03
JP603 | Pin Head 1x3 | - | Trigger Level | - | - | - | ~ | Pin_Headers:Pin_Header_Straight_1x03
JP604 | Pin Head 1x3 | - | Trigger Level | - | - | - | ~ | Pin_Headers:Pin_Header_Straight_1x03
K401 | RELAY_1C | - | ign batt relay | Omron | G5LE-14 DC5 | SPDT (1 Form C) 5VDC Coil | https://github.com/psas/launch-tower/blob/master/ltc3/doc/datasheets/Omron-G5LE-Single_Pole_10A_Power_Relay.pdf | LTC3:G5LE-14
K402 | RELAY_1C | - | ign relay | Omron | G5LE-14 DC5 | SPDT (1 Form C) 5VDC Coil | https://github.com/psas/launch-tower/blob/master/ltc3/doc/datasheets/Omron-G5LE-Single_Pole_10A_Power_Relay.pdf | LTC3:G5LE-14
M401 | 10A | - | OFF-BOARD | TE | W28-XQ1A-10 | 10A 250VAC 32VDC | https://github.com/psas/launch-tower/blob/master/ltc3/doc/datasheets/TE-W28_Series-Push_To_Reset_Fuseholder_Type_Thermal_Circuit_Breaker.pdf | ~
M501 | 1A | - | OFF-BOARD | TE | W28-XQ1A-1 | 1A 250VAC 32VDC | https://github.com/psas/launch-tower/blob/master/ltc3/doc/datasheets/TE-W28_Series-Push_To_Reset_Fuseholder_Type_Thermal_Circuit_Breaker.pdf | ~
M502 | 1A | - | OFF-BOARD | TE | W28-XQ1A-1 | 1A 250VAC 32VDC | https://github.com/psas/launch-tower/blob/master/ltc3/doc/datasheets/TE-W28_Series-Push_To_Reset_Fuseholder_Type_Thermal_Circuit_Breaker.pdf | ~
M503 | 1A | - | OFF-BOARD | TE | W28-XQ1A-1 | 1A 250VAC 32VDC | https://github.com/psas/launch-tower/blob/master/ltc3/doc/datasheets/TE-W28_Series-Push_To_Reset_Fuseholder_Type_Thermal_Circuit_Breaker.pdf | ~
M504 | 1A | - | OFF-BOARD | TE | W28-XQ1A-1 | 1A 250VAC 32VDC | https://github.com/psas/launch-tower/blob/master/ltc3/doc/datasheets/TE-W28_Series-Push_To_Reset_Fuseholder_Type_Thermal_Circuit_Breaker.pdf | ~
P201 | MicroFit header | - | DC_IN (from Cell Prot.) | Molex | 43045-0428 | 4 pos vertical header | https://github.com/psas/launch-tower/blob/master/ltc3/doc/datasheets/connectors/Molex-43045-Micro_Fit_3_dual_row_vertical_through_hole_header.pdf | Connectors_Molex:Molex_Microfit3_Header_02x02_Straight_43045-0428
P202 | XH header | - | to front panel; mates to P203 | JST | B2B-XH-A(LF)(SN) | 2 pos vertical header | https://github.com/psas/launch-tower/blob/master/ltc3/doc/datasheets/connectors/JST-XH-2.5mm_pitch_Disconnectable_Crimp_style_connectors.pdf | Connectors_JST:JST_XH_B02B-XH-A_02x2.50mm_Straight
P203 | XH connector | - | OFF-BOARD; mates to P202 | JST | XHP-2 | 2 pos connector | https://github.com/psas/launch-tower/blob/master/ltc3/doc/datasheets/connectors/JST-XH-2.5mm_pitch_Disconnectable_Crimp_style_connectors.pdf | ~
P204 | Pin Head 1x2 | - | - | - | - | - | ~ | Pin_Headers:Pin_Header_Straight_1x02
P205 | Pin Head 1x2 | - | - | - | - | - | ~ | Pin_Headers:Pin_Header_Straight_1x02
P206 | Pin Head 1x2 | - | - | - | - | - | ~ | Pin_Headers:Pin_Header_Straight_1x02
P301 | BeagleBone_Black_Expansion_Header_P8 | - | - | - | - | - | ~ | Pin_Headers:Pin_Header_Straight_2x23
P302 | BeagleBone_Black_Expansion_Header_P9 | - | - | - | - | - | ~ | Pin_Headers:Pin_Header_Straight_2x23
P303 | XH header | - | to charge controller | JST | B4B-XH-A(LF)(SN) | 4 pos vertical header | https://github.com/psas/launch-tower/blob/master/ltc3/doc/datasheets/connectors/JST-XH-2.5mm_pitch_Disconnectable_Crimp_style_connectors.pdf | Connectors_JST:JST_XH_B04B-XH-A_04x2.50mm_Straight
P304 | XH header | - | to cell protection | JST | B4B-XH-A(LF)(SN) | 4 pos vertical header | https://github.com/psas/launch-tower/blob/master/ltc3/doc/datasheets/connectors/JST-XH-2.5mm_pitch_Disconnectable_Crimp_style_connectors.pdf | Connectors_JST:JST_XH_B04B-XH-A_04x2.50mm_Straight
P401 | MicroFit header | - | to ignition batt | Molex | 43045-0428 | 4 pos vertical header | https://github.com/psas/launch-tower/blob/master/ltc3/doc/datasheets/connectors/Molex-43045-Micro_Fit_3_dual_row_vertical_through_hole_header.pdf | Connectors_Molex:Molex_Microfit3_Header_02x02_Straight_43045-0428
P402 | MicroFit header | - | to front panel; mates to P403 | Molex | 43045-0228 | 2 pos vertical header | https://github.com/psas/launch-tower/blob/master/ltc3/doc/datasheets/connectors/Molex-43045-Micro_Fit_3_dual_row_vertical_through_hole_header.pdf | Connectors_Molex:Molex_Microfit3_Header_02x01_Straight_43045-0228
P403 | MicroFit connector | - | OFF-BOARD; mates to P402 | Molex | 43025-0200 | 2 pos connector | https://github.com/psas/launch-tower/blob/master/ltc3/doc/datasheets/connectors/Molex-Micro_Fit_3_Family.pdf | ~
P404 | MicroFit header | - | to front panel; mates to P405 | Molex | 43045-0228 | 2 pos vertical header | https://github.com/psas/launch-tower/blob/master/ltc3/doc/datasheets/connectors/Molex-43045-Micro_Fit_3_dual_row_vertical_through_hole_header.pdf | Connectors_Molex:Molex_Microfit3_Header_02x01_Straight_43045-0228
P405 | MicroFit connector | - | OFF-BOARD; mates to P404 | Molex | 43025-0200 | 2 pos connector | https://github.com/psas/launch-tower/blob/master/ltc3/doc/datasheets/connectors/Molex-Micro_Fit_3_Family.pdf | ~
P406 | XH header | - | to front panel; mates to P407 | JST | B4B-XH-A(LF)(SN) | 4 pos vertical header | https://github.com/psas/launch-tower/blob/master/ltc3/doc/datasheets/connectors/JST-XH-2.5mm_pitch_Disconnectable_Crimp_style_connectors.pdf | Connectors_JST:JST_XH_B04B-XH-A_04x2.50mm_Straight
P407 | XH connector | - | OFF-BOARD; mates to P406 | JST | XHP-4 | 4 pos connector | https://github.com/psas/launch-tower/blob/master/ltc3/doc/datasheets/connectors/JST-XH-2.5mm_pitch_Disconnectable_Crimp_style_connectors.pdf | ~
P408 | MicroFit header | - | to front panel | Molex | 43045-1028 | 10 pos vertical header | https://github.com/psas/launch-tower/blob/master/ltc3/doc/datasheets/connectors/Molex-43045-Micro_Fit_3_dual_row_vertical_through_hole_header.pdf | Connectors_Molex:Molex_Microfit3_Header_02x05_Straight_43045-1028
P409 | CONN_01x02 | - | OFF-BOARD; to away box | - | - | - | ~ | ~
P501 | MicroFit header | - | to front panel; mates to P503 | Molex | 43045-0828 | 8 pos vertical header | https://github.com/psas/launch-tower/blob/master/ltc3/doc/datasheets/connectors/Molex-43045-Micro_Fit_3_dual_row_vertical_through_hole_header.pdf | Connectors_Molex:Molex_Microfit3_Header_02x04_Straight_43045-0828
P502 | MicroFit header | - | to front panel; mates to P502 | Molex | 43045-0828 | 8 pos vertical header | https://github.com/psas/launch-tower/blob/master/ltc3/doc/datasheets/connectors/Molex-43045-Micro_Fit_3_dual_row_vertical_through_hole_header.pdf | Connectors_Molex:Molex_Microfit3_Header_02x04_Straight_43045-0828
P503 | MicroFit connector | - | OFF-BOARD; mates to P501 | Molex | 43025-0800 | 8 pos connector | https://github.com/psas/launch-tower/blob/master/ltc3/doc/datasheets/connectors/Molex-Micro_Fit_3_Family.pdf | ~
P504 | MicroFit connector | - | OFF-BOARD; mates to P502 | Molex | 43025-0800 | 8 pos connector | https://github.com/psas/launch-tower/blob/master/ltc3/doc/datasheets/connectors/Molex-Micro_Fit_3_Family.pdf | ~
P505 | PowerPole | - | OFF-BOARD | Anderson | 1327G6 | - | https://github.com/psas/launch-tower/blob/master/ltc3/doc/datasheets/connectors/Anderson-Powerpole_Connectors_PP15_to_PP45.pdf | ~
P506 | PowerPole | - | OFF-BOARD | Anderson | 1327 | - | https://github.com/psas/launch-tower/blob/master/ltc3/doc/datasheets/connectors/Anderson-Powerpole_Connectors_PP15_to_PP45.pdf | ~
P507 | PowerPole | - | OFF-BOARD | Anderson | 1327G6 | - | https://github.com/psas/launch-tower/blob/master/ltc3/doc/datasheets/connectors/Anderson-Powerpole_Connectors_PP15_to_PP45.pdf | ~
P508 | PowerPole | - | OFF-BOARD | Anderson | 1327 | - | https://github.com/psas/launch-tower/blob/master/ltc3/doc/datasheets/connectors/Anderson-Powerpole_Connectors_PP15_to_PP45.pdf | ~
P509 | PowerPole | - | OFF-BOARD | Anderson | 1327G6 | - | https://github.com/psas/launch-tower/blob/master/ltc3/doc/datasheets/connectors/Anderson-Powerpole_Connectors_PP15_to_PP45.pdf | ~
P510 | PowerPole | - | OFF-BOARD | Anderson | 1327 | - | https://github.com/psas/launch-tower/blob/master/ltc3/doc/datasheets/connectors/Anderson-Powerpole_Connectors_PP15_to_PP45.pdf | ~
P511 | PowerPole | - | OFF-BOARD | Anderson | 1327G6 | - | https://github.com/psas/launch-tower/blob/master/ltc3/doc/datasheets/connectors/Anderson-Powerpole_Connectors_PP15_to_PP45.pdf | ~
P512 | PowerPole | - | OFF-BOARD | Anderson | 1327 | - | https://github.com/psas/launch-tower/blob/master/ltc3/doc/datasheets/connectors/Anderson-Powerpole_Connectors_PP15_to_PP45.pdf | ~
P601 | MicroFit header | - | to front panel | Molex | 43045-0828 | 8 pos vertical header | https://github.com/psas/launch-tower/blob/master/ltc3/doc/datasheets/connectors/Molex-43045-Micro_Fit_3_dual_row_vertical_through_hole_header.pdf | Connectors_Molex:Molex_Microfit3_Header_02x04_Straight_43045-0828
P602 | MicroFit connector | - | OFF-BOARD; mates to P605 | Molex | 43025-0800 | 8 pos connector | https://github.com/psas/launch-tower/blob/master/ltc3/doc/datasheets/connectors/Molex-Micro_Fit_3_Family.pdf | ~
P603 | PowerPole | - | OFF-BOARD | Anderson | 1327G6 | - | https://github.com/psas/launch-tower/blob/master/ltc3/doc/datasheets/connectors/Anderson-Powerpole_Connectors_PP15_to_PP45.pdf | ~
P604 | PowerPole | - | OFF-BOARD | Anderson | 1327 | - | https://github.com/psas/launch-tower/blob/master/ltc3/doc/datasheets/connectors/Anderson-Powerpole_Connectors_PP15_to_PP45.pdf | ~
P605 | PowerPole | - | OFF-BOARD | Anderson | 1327G6 | - | https://github.com/psas/launch-tower/blob/master/ltc3/doc/datasheets/connectors/Anderson-Powerpole_Connectors_PP15_to_PP45.pdf | ~
P606 | PowerPole | - | OFF-BOARD | Anderson | 1327 | - | https://github.com/psas/launch-tower/blob/master/ltc3/doc/datasheets/connectors/Anderson-Powerpole_Connectors_PP15_to_PP45.pdf | ~
P607 | PowerPole | - | OFF-BOARD | Anderson | 1327G6 | - | https://github.com/psas/launch-tower/blob/master/ltc3/doc/datasheets/connectors/Anderson-Powerpole_Connectors_PP15_to_PP45.pdf | ~
P608 | PowerPole | - | OFF-BOARD | Anderson | 1327 | - | https://github.com/psas/launch-tower/blob/master/ltc3/doc/datasheets/connectors/Anderson-Powerpole_Connectors_PP15_to_PP45.pdf | ~
P609 | PowerPole | - | OFF-BOARD | Anderson | 1327G6 | - | https://github.com/psas/launch-tower/blob/master/ltc3/doc/datasheets/connectors/Anderson-Powerpole_Connectors_PP15_to_PP45.pdf | ~
P610 | PowerPole | - | OFF-BOARD | Anderson | 1327 | - | https://github.com/psas/launch-tower/blob/master/ltc3/doc/datasheets/connectors/Anderson-Powerpole_Connectors_PP15_to_PP45.pdf | ~
Q202 | BSS138 | - | - | Fairchild | BSS138 | MOSFET N-CH 50V 220MA | https://github.com/psas/launch-tower/blob/master/ltc3/doc/datasheets/semiconductors/Fairchild-BSS138-N_Channel_Logic_Level_Enhancement_Mode_FET.pdf | TO_SOT_Packages_SMD:SOT-23
Q203 | BSS138 | - | - | Fairchild | BSS138 | MOSFET N-CH 50V 220MA | https://github.com/psas/launch-tower/blob/master/ltc3/doc/datasheets/semiconductors/Fairchild-BSS138-N_Channel_Logic_Level_Enhancement_Mode_FET.pdf | TO_SOT_Packages_SMD:SOT-23
Q401 | PMV45EN | - | - | NXP | PMV45EN2R | MOSFET N-CH 30V | https://github.com/psas/launch-tower/blob/master/ltc3/doc/datasheets/semiconductors/NXP-PMV45EN-N_Channel_TrenchMOS_logic_level_FET.pdf | TO_SOT_Packages_SMD:SOT-23
Q402 | PMV45EN | - | - | NXP | PMV45EN2R | MOSFET N-CH 30V | https://github.com/psas/launch-tower/blob/master/ltc3/doc/datasheets/semiconductors/NXP-PMV45EN-N_Channel_TrenchMOS_logic_level_FET.pdf | TO_SOT_Packages_SMD:SOT-23
Q403 | PMV45EN | - | - | NXP | PMV45EN2R | MOSFET N-CH 30V | https://github.com/psas/launch-tower/blob/master/ltc3/doc/datasheets/semiconductors/NXP-PMV45EN-N_Channel_TrenchMOS_logic_level_FET.pdf | TO_SOT_Packages_SMD:SOT-23
Q404 | PMV45EN | - | - | NXP | PMV45EN2R | MOSFET N-CH 30V | https://github.com/psas/launch-tower/blob/master/ltc3/doc/datasheets/semiconductors/NXP-PMV45EN-N_Channel_TrenchMOS_logic_level_FET.pdf | TO_SOT_Packages_SMD:SOT-23
Q405 | PMV45EN | - | - | NXP | PMV45EN2R | MOSFET N-CH 30V | https://github.com/psas/launch-tower/blob/master/ltc3/doc/datasheets/semiconductors/NXP-PMV45EN-N_Channel_TrenchMOS_logic_level_FET.pdf | TO_SOT_Packages_SMD:SOT-23
Q501 | PMV45EN | - | - | NXP | PMV45EN2R | MOSFET N-CH 30V | https://github.com/psas/launch-tower/blob/master/ltc3/doc/datasheets/semiconductors/NXP-PMV45EN-N_Channel_TrenchMOS_logic_level_FET.pdf | TO_SOT_Packages_SMD:SOT-23
Q502 | PMV45EN | - | - | NXP | PMV45EN2R | MOSFET N-CH 30V | https://github.com/psas/launch-tower/blob/master/ltc3/doc/datasheets/semiconductors/NXP-PMV45EN-N_Channel_TrenchMOS_logic_level_FET.pdf | TO_SOT_Packages_SMD:SOT-23
Q503 | PMV45EN | - | - | NXP | PMV45EN2R | MOSFET N-CH 30V | https://github.com/psas/launch-tower/blob/master/ltc3/doc/datasheets/semiconductors/NXP-PMV45EN-N_Channel_TrenchMOS_logic_level_FET.pdf | TO_SOT_Packages_SMD:SOT-23
Q504 | PMV45EN | - | - | NXP | PMV45EN2R | MOSFET N-CH 30V | https://github.com/psas/launch-tower/blob/master/ltc3/doc/datasheets/semiconductors/NXP-PMV45EN-N_Channel_TrenchMOS_logic_level_FET.pdf | TO_SOT_Packages_SMD:SOT-23
Q601 | PMV45EN | - | - | NXP | PMV45EN2R | MOSFET N-CH 30V | https://github.com/psas/launch-tower/blob/master/ltc3/doc/datasheets/semiconductors/NXP-PMV45EN-N_Channel_TrenchMOS_logic_level_FET.pdf | TO_SOT_Packages_SMD:SOT-23
Q602 | PMV45EN | - | - | NXP | PMV45EN2R | MOSFET N-CH 30V | https://github.com/psas/launch-tower/blob/master/ltc3/doc/datasheets/semiconductors/NXP-PMV45EN-N_Channel_TrenchMOS_logic_level_FET.pdf | TO_SOT_Packages_SMD:SOT-23
Q603 | PMV45EN | - | - | NXP | PMV45EN2R | MOSFET N-CH 30V | https://github.com/psas/launch-tower/blob/master/ltc3/doc/datasheets/semiconductors/NXP-PMV45EN-N_Channel_TrenchMOS_logic_level_FET.pdf | TO_SOT_Packages_SMD:SOT-23
Q604 | PMV45EN | - | - | NXP | PMV45EN2R | MOSFET N-CH 30V | https://github.com/psas/launch-tower/blob/master/ltc3/doc/datasheets/semiconductors/NXP-PMV45EN-N_Channel_TrenchMOS_logic_level_FET.pdf | TO_SOT_Packages_SMD:SOT-23
R201 | 60m | 1W 1% | - | Yageo | PE2512FKE7W0R06L | 1% 2W | ~ | Resistors_SMD:R_2512
R202 | 21k | 1% 50mW | - | Yageo | RC0805FR-0721KL | 1% 1/8W | ~ | Resistors_SMD:R_0805
R203 | 60m | 1W 1% | - | Yageo | PE2512FKE7W0R06L | 1% 2W | ~ | Resistors_SMD:R_2512
R204 | 383k | 1% 50mW | - | Yageo | RC0805FR-07383KL | 1% 1/8W | ~ | Resistors_SMD:R_0805
R205 | 60m | 1W 1% | - | Yageo | PE2512FKE7W0R06L | 1% 2W | ~ | Resistors_SMD:R_2512
R206 | 2.87k | 1% 50mW | datasheet-spec’d 2.91k is unavailable | Panasonic | ERJ-6ENF2871V | 1% 1/8W 100ppm | ~ | Resistors_SMD:R_0805
R207 | 20k | - | - | Yageo | RC0805FR-0720KL | 1% 1/8W | ~ | Resistors_SMD:R_0805
R208 | 20k | - | - | Yageo | RC0805FR-0720KL | 1% 1/8W | ~ | Resistors_SMD:R_0805
R209 | 10k | - | - | Yageo | RC0805FR-0710KL | 1% 1/8W | ~ | Resistors_SMD:R_0805
R210 | 10k | - | - | Yageo | RC0805FR-0710KL | 1% 1/8W | ~ | Resistors_SMD:R_0805
R211 | 36k | - | - | Yageo | RC0805FR-0736KL | 1% 1/8W | ~ | Resistors_SMD:R_0805
R212 | 36k | - | - | Yageo | RC0805FR-0736KL | 1% 1/8W | ~ | Resistors_SMD:R_0805
R213 | 10k | - | - | Yageo | RC0805FR-0710KL | 1% 1/8W | ~ | Resistors_SMD:R_0805
R214 | 10k | - | - | Yageo | RC0805FR-0710KL | 1% 1/8W | ~ | Resistors_SMD:R_0805
R301 | 5.6k | - | - | Yageo | RC0805FR-075K6L | 1% 1/8W | ~ | Resistors_SMD:R_0805
R302 | 5.6k | - | - | Yageo | RC0805FR-075K6L | 1% 1/8W | ~ | Resistors_SMD:R_0805
R303 | 5.6k | - | - | Yageo | RC0805FR-075K6L | 1% 1/8W | ~ | Resistors_SMD:R_0805
R304 | 5.6k | - | - | Yageo | RC0805FR-075K6L | 1% 1/8W | ~ | Resistors_SMD:R_0805
R401 | 62k | - | - | Yageo | RC0805FR-0762KL | 1% 1/8W | ~ | Resistors_SMD:R_0805
R402 | 10k | - | - | Yageo | RC0805FR-0710KL | 1% 1/8W | ~ | Resistors_SMD:R_0805
R403 | 100k | - | - | Yageo | RC0805FR-07100KL | 1% 1/8W | ~ | Resistors_SMD:R_0805
R404 | 120 | - | - | Yageo | RC0805FR-07120RL | 1% 1/8W | ~ | Resistors_SMD:R_0805
R405 | 10k | - | - | Yageo | RC0805FR-0710KL | 1% 1/8W | ~ | Resistors_SMD:R_0805
R406 | 100 | - | - | Yageo | RC0805FR-07100RL | 1% 1/8W | ~ | Resistors_SMD:R_0805
R407 | 500k | - | - | Yageo | RC0805FR-07510KL | 1% 1/8W | ~ | Resistors_SMD:R_0805
R408 | NP | - | - | - | - | - | ~ | Resistors_SMD:R_0805
R409 | 10k | - | - | Yageo | RC0805FR-0710KL | 1% 1/8W | ~ | Resistors_SMD:R_0805
R410 | 5.6k | - | - | Yageo | RC0805FR-075K6L | 1% 1/8W | ~ | Resistors_SMD:R_0805
R411 | 62k | - | - | Yageo | RC0805FR-0762KL | 1% 1/8W | ~ | Resistors_SMD:R_0805
R412 | 240 | - | - | Yageo | RC0805FR-07240RL | 1% 1/8W | ~ | Resistors_SMD:R_0805
R413 | 1.5k | - | - | Yageo | RC0805FR-071K5L | 1% 1/8W | ~ | Resistors_SMD:R_0805
R414 | 10k | - | - | Yageo | RC0805FR-0710KL | 1% 1/8W | ~ | Resistors_SMD:R_0805
R415 | 100k | - | - | Yageo | RC0805FR-07100KL | 1% 1/8W | ~ | Resistors_SMD:R_0805
R416 | 10k | - | - | Yageo | RC0805FR-0710KL | 1% 1/8W | ~ | Resistors_SMD:R_0805
R417 | 10k | - | - | Yageo | RC0805FR-0710KL | 1% 1/8W | ~ | Resistors_SMD:R_0805
R418 | 10k | - | - | Yageo | RC0805FR-0710KL | 1% 1/8W | ~ | Resistors_SMD:R_0805
R419 | 5.1k | - | - | Yageo | RC0805FR-075K1L | 1% 1/8W | ~ | Resistors_SMD:R_0805
R420 | 240 | - | - | Yageo | RC0805FR-07240RL | 1% 1/8W | ~ | Resistors_SMD:R_0805
R421 | 10k | - | - | Yageo | RC0805FR-0710KL | 1% 1/8W | ~ | Resistors_SMD:R_0805
R422 | 5.1k | - | - | Yageo | RC0805FR-075K1L | 1% 1/8W | ~ | Resistors_SMD:R_0805
R423 | 0 | - | Dialight LED may not require ext. R | Yageo | RC0805JR-070RL | 1/8W | ~ | Resistors_SMD:R_0805
R424 | 0 | - | Dialight LED may not require ext. R | Yageo | RC0805JR-070RL | 1/8W | ~ | Resistors_SMD:R_0805
R425 | 0 | - | Dialight LED may not require ext. R | Yageo | RC0805JR-070RL | 1/8W | ~ | Resistors_SMD:R_0805
R501 | 270 | - | - | Yageo | RC0805FR-07270RL | 1% 1/8W | ~ | Resistors_SMD:R_0805
R502 | 270 | - | - | Yageo | RC0805FR-07270RL | 1% 1/8W | ~ | Resistors_SMD:R_0805
R503 | 51k | - | - | Yageo | RC0805FR-0751KL | 1% 1/8W | ~ | Resistors_SMD:R_0805
R504 | 51k | - | - | Yageo | RC0805FR-0751KL | 1% 1/8W | ~ | Resistors_SMD:R_0805
R505 | 10k | - | - | Yageo | RC0805FR-0710KL | 1% 1/8W | ~ | Resistors_SMD:R_0805
R506 | 10k | - | - | Yageo | RC0805FR-0710KL | 1% 1/8W | ~ | Resistors_SMD:R_0805
R507 | 270 | - | - | Yageo | RC0805FR-07270RL | 1% 1/8W | ~ | Resistors_SMD:R_0805
R508 | 270 | - | - | Yageo | RC0805FR-07270RL | 1% 1/8W | ~ | Resistors_SMD:R_0805
R509 | 51k | - | - | Yageo | RC0805FR-0751KL | 1% 1/8W | ~ | Resistors_SMD:R_0805
R510 | 51k | - | - | Yageo | RC0805FR-0751KL | 1% 1/8W | ~ | Resistors_SMD:R_0805
R511 | 10k | - | - | Yageo | RC0805FR-0710KL | 1% 1/8W | ~ | Resistors_SMD:R_0805
R512 | 10k | - | - | Yageo | RC0805FR-0710KL | 1% 1/8W | ~ | Resistors_SMD:R_0805
R601 | 270 | - | - | Yageo | RC0805FR-07270RL | 1% 1/8W | ~ | Resistors_SMD:R_0805
R602 | 270 | - | - | Yageo | RC0805FR-07270RL | 1% 1/8W | ~ | Resistors_SMD:R_0805
R603 | 10k | - | - | Yageo | RC0805FR-0710KL | 1% 1/8W | ~ | Resistors_SMD:R_0805
R604 | 10k | - | - | Yageo | RC0805FR-0710KL | 1% 1/8W | ~ | Resistors_SMD:R_0805
R605 | 270 | - | - | Yageo | RC0805FR-07270RL | 1% 1/8W | ~ | Resistors_SMD:R_0805
R606 | 270 | - | - | Yageo | RC0805FR-07270RL | 1% 1/8W | ~ | Resistors_SMD:R_0805
R607 | 10k | - | - | Yageo | RC0805FR-0710KL | 1% 1/8W | ~ | Resistors_SMD:R_0805
R608 | 10k | - | - | Yageo | RC0805FR-0710KL | 1% 1/8W | ~ | Resistors_SMD:R_0805
R609 | 100 | - | - | Yageo | RC0805FR-07100RL | 1% 1/8W | ~ | Resistors_SMD:R_0805
R610 | 100 | - | - | Yageo | RC0805FR-07100RL | 1% 1/8W | ~ | Resistors_SMD:R_0805
R611 | 100 | - | - | Yageo | RC0805FR-07100RL | 1% 1/8W | ~ | Resistors_SMD:R_0805
R612 | 100 | - | - | Yageo | RC0805FR-07100RL | 1% 1/8W | ~ | Resistors_SMD:R_0805
SW201 | SPST | - | OFF-BOARD | - | - | - | ~ | ~
SW401 | SPST | - | OFF-BOARD | - | - | - | ~ | ~
SW501 | MOMENTARY | - | ENABLE | Panasonic | EVQ-Q2K03W | Tactile SPST-NO Top Actuated SMD | https://github.com/psas/launch-tower/blob/master/ltc3/doc/datasheets/Panasonic-EVQQ2-6mm_Square_Thin_SMD_Touch_Switches.pdf | Buttons_Switches_SMD:SW_SPST_EVQQ2
SW502 | MOMENTARY | - | ENABLE | Panasonic | EVQ-Q2K03W | Tactile SPST-NO Top Actuated SMD | https://github.com/psas/launch-tower/blob/master/ltc3/doc/datasheets/Panasonic-EVQQ2-6mm_Square_Thin_SMD_Touch_Switches.pdf | Buttons_Switches_SMD:SW_SPST_EVQQ2
SW503 | MOMENTARY | - | ENABLE | Panasonic | EVQ-Q2K03W | Tactile SPST-NO Top Actuated SMD | https://github.com/psas/launch-tower/blob/master/ltc3/doc/datasheets/Panasonic-EVQQ2-6mm_Square_Thin_SMD_Touch_Switches.pdf | Buttons_Switches_SMD:SW_SPST_EVQQ2
SW504 | MOMENTARY | - | ENABLE | Panasonic | EVQ-Q2K03W | Tactile SPST-NO Top Actuated SMD | https://github.com/psas/launch-tower/blob/master/ltc3/doc/datasheets/Panasonic-EVQQ2-6mm_Square_Thin_SMD_Touch_Switches.pdf | Buttons_Switches_SMD:SW_SPST_EVQQ2
SW601 | MOMENTARY | - | ENABLE | Panasonic | EVQ-Q2K03W | Tactile SPST-NO Top Actuated SMD | https://github.com/psas/launch-tower/blob/master/ltc3/doc/datasheets/Panasonic-EVQQ2-6mm_Square_Thin_SMD_Touch_Switches.pdf | Buttons_Switches_SMD:SW_SPST_EVQQ2
SW602 | MOMENTARY | - | ENABLE | Panasonic | EVQ-Q2K03W | Tactile SPST-NO Top Actuated SMD | https://github.com/psas/launch-tower/blob/master/ltc3/doc/datasheets/Panasonic-EVQQ2-6mm_Square_Thin_SMD_Touch_Switches.pdf | Buttons_Switches_SMD:SW_SPST_EVQQ2
SW603 | MOMENTARY | - | ENABLE | Panasonic | EVQ-Q2K03W | Tactile SPST-NO Top Actuated SMD | https://github.com/psas/launch-tower/blob/master/ltc3/doc/datasheets/Panasonic-EVQQ2-6mm_Square_Thin_SMD_Touch_Switches.pdf | Buttons_Switches_SMD:SW_SPST_EVQQ2
SW604 | MOMENTARY | - | ENABLE | Panasonic | EVQ-Q2K03W | Tactile SPST-NO Top Actuated SMD | https://github.com/psas/launch-tower/blob/master/ltc3/doc/datasheets/Panasonic-EVQQ2-6mm_Square_Thin_SMD_Touch_Switches.pdf | Buttons_Switches_SMD:SW_SPST_EVQQ2
U201 | PTN78020W | - | - | Texas Instruments | PTN78020WAH | REG SW 2.5-12.6V 6A | https://github.com/psas/launch-tower/blob/master/ltc3/doc/datasheets/TI-PTN78020-6A_Wide_Input_Adjustable_Switching_Regulator.pdf | LTC3:PTN78020W
U202 | LTC2991 | - | - | Linear | LTC2991CMS#PBF | - | https://github.com/psas/launch-tower/blob/master/ltc3/doc/datasheets/LTC299x/Linear-LTC2991-Octal_I2C_Voltage_Current_and_Temp_Monitor.pdf | LTC3:MSOP-16
U203 | PTN78020H | - | - | Texas Instruments | PTN78020HAH | REG SW 11.85-22V 6A | https://github.com/psas/launch-tower/blob/master/ltc3/doc/datasheets/TI-PTN78020-6A_Wide_Input_Adjustable_Switching_Regulator.pdf | LTC3:PTN78020W
U204 | PTN78020H | - | - | Texas Instruments | PTN78020HAH | REG SW 11.85-22V 6A | https://github.com/psas/launch-tower/blob/master/ltc3/doc/datasheets/TI-PTN78020-6A_Wide_Input_Adjustable_Switching_Regulator.pdf | LTC3:PTN78020W
U301 | CAT24C256 | - | - | ON Semi | CAT24C256YI-GT3 | EEPROM 256KBIT 400KHZ | https://github.com/psas/launch-tower/blob/master/ltc3/doc/datasheets/ON_Semi-CAT24C256-256_kb_I2C_CMOS_Serial_EEPROM.pdf | Housings_SSOP:TSSOP-8_4.4x3mm_Pitch0.65mm
U401 | CD74HC14 | - | - | Texas Instruments | CD74HC14PWR | Inverter IC 6 Channel Schmitt | https://github.com/psas/launch-tower/blob/master/ltc3/doc/datasheets/logic/TI-CD74HC14-High_Speed_CMOS_Logic_Hex_Inverting_Schmitt_Trigger.pdf | Housings_SSOP:TSSOP-14_4.4x5mm_Pitch0.65mm
U402 | SN65220DBV | - | - | Texas Instruments | SN65220DBVR | TVS | https://github.com/psas/launch-tower/blob/master/ltc3/doc/datasheets/semiconductors/TI-SNx52x0-USB_Port_Transient_Suppressors.pdf | TO_SOT_Packages_SMD:SOT-23-6
U403 | SN74AHC1G08 | - | - | Texas Instruments | SN74AHC1G08DCKR | 2 input AND gate | https://github.com/psas/launch-tower/blob/master/ltc3/doc/datasheets/logic/TI-SN74AHC1G08-Single_Two_Input_Positive_AND_Gate.pdf | TO_SOT_Packages_SMD:SC-70-5
U404 | TLP3542 | - | - | Toshiba | TLP3542 | - | https://github.com/psas/launch-tower/blob/master/ltc3/doc/datasheets/semiconductors/Toshiba-TLP3542-Photo_Relay.pdf | Housings_DIP:DIP-6_W7.62mm
U501 | TLP3542 | - | - | Toshiba | TLP3542 | - | https://github.com/psas/launch-tower/blob/master/ltc3/doc/datasheets/semiconductors/Toshiba-TLP3542-Photo_Relay.pdf | Housings_DIP:DIP-6_W7.62mm
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

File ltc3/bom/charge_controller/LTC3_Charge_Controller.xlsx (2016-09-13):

Refs | value | Spec | Note | Mfg_Name | Mfg_PN | Mfg_Description | datasheet | footprint
C1 | 0.33μ | 50V X7R | - | Murata | GRM21AR72A334KAC5L | 100V X7R 10% | ~ | Capacitors_SMD:C_0805
C2 | 33μ | 35V | - | Nichicon | UUX2A330MNL1GS | alum. Electrolytic, 100V 20% | ~ | Capacitors_SMD:c_elec_10x10
C3 | 0.1μ | - | - | Murata | GCM21BR72A104KA37L | 100V X7R 10% | ~ | Capacitors_SMD:C_0805
C4 | 33μ | 35V | - | Nichicon | UUX2A330MNL1GS | alum. Electrolytic, 100V 20% | ~ | Capacitors_SMD:c_elec_10x10
C5 | 33μ | 35V | - | Nichicon | UUX2A330MNL1GS | alum. Electrolytic, 100V 20% | ~ | Capacitors_SMD:c_elec_10x10
C6 | 4.7μ | 15V | - | Murata | GRM21BR71C475KA73L | 16V X7R 10% | ~ | Capacitors_SMD:C_0805
C7 | 4.7μ | 15V | - | Murata | GRM21BR71C475KA73L | 16V X7R 10% | ~ | Capacitors_SMD:C_0805
C8 | 0.01μ | - | - | Murata | GRM216R71H103JA01D | 50V X7R 5% | ~ | Capacitors_SMD:C_0805
C9 | 2.2μ | 50V X7R | - | Murata | GRM32ER72A225KA35L | 100V X7R 10% | ~ | Capacitors_SMD:C_1210
C10 | 0.01μ | - | - | Murata | GRM216R71H103JA01D | 50V X7R 5% | ~ | Capacitors_SMD:C_0805
C11 | 2.2μ | 50V X7R | - | Murata | GRM32ER72A225KA35L | 100V X7R 10% | ~ | Capacitors_SMD:C_1210
C12 | 2.2μ | 50V X7R | - | Murata | GRM32ER72A225KA35L | 100V X7R 10% | ~ | Capacitors_SMD:C_1210
C13 | 220n | 10V | - | Murata | GRM21BR71H224KA01L | 50V X7R 10% | ~ | Capacitors_SMD:C_0805
C14 | 2.2μ | 50V X7R | - | Murata | GRM32ER72A225KA35L | 100V X7R 10% | ~ | Capacitors_SMD:C_1210
C15 | 220n | 10V | - | Murata | GRM21BR71H224KA01L | 50V X7R 10% | ~ | Capacitors_SMD:C_0805
C16 | 8.2n | 10V | - | Murata | GRM21BR71H823KA01L | 50V X7R 10% | ~ | Capacitors_SMD:C_0805
C17 | 220p | 10V | - | Yago | CC0805KRX7R9BB221 | 50V X7R 10% | ~ | Capacitors_SMD:C_0805
C18 | 470n | 10V | - | Murata | GRM21BR71H474KA88L | 50V X7R 10% | ~ | Capacitors_SMD:C_0805
C19 | 68n | 10V | - | Murata | GRM219R71E683KA01D | 25V X7R 10% | ~ | Capacitors_SMD:C_0805
C20 | 2.2μ | 50V X7R | - | Murata | GRM32ER72A225KA35L | 100V X7R 10% | ~ | Capacitors_SMD:C_1210
C21 | 2.2μ | 50V X7R | - | Murata | GRM32ER72A225KA35L | 100V X7R 10% | ~ | Capacitors_SMD:C_1210
C22 | 0.001μ | - | - | Murata | GRM216R71H102JA01D | 50V X7R 5% | ~ | Capacitors_SMD:C_0805
C23 | 0.001μ | - | - | Murata | GRM216R71H102JA01D | 50V X7R 5% | ~ | Capacitors_SMD:C_0805
C24 | 4.7μ | 10V | - | Murata | GRM21BR71C475KA73L | 16V X7R 10% | ~ | Capacitors_SMD:C_0805
C25 | 1μ | 10V | - | Murata | GRM21BR71E105KA99K | 25V X7R 10% | ~ | Capacitors_SMD:C_0805
C26 | 0.1μ | - | - | Murata | GCM21BR72A104KA37L | 100V X7R 10% | ~ | Capacitors_SMD:C_0805
C27 | 0.18μ | - | - | Murata | GRM21BR71H184KA01L | 50V X7R 10% | ~ | Capacitors_SMD:C_0805
C28 | 4.7μ | 75V | - | Murata | GRM55ER72A475KA01L | 100V X7R 10% | ~ | Capacitors_SMD:C_2220
C29 | 4.7μ | 75V | - | Murata | GRM55ER72A475KA01L | 100V X7R 10% | ~ | Capacitors_SMD:C_2220
C30 | 1μ | 75V | - | Murata | GRJ21BC72A105KE11L | 100V X7S 10% | ~ | Capacitors_SMD:C_0805
C31 | 0.1μ | 75V X7R | - | Murata | GCM21BR72A104KA37L | 100V X7R 10% | ~ | Capacitors_SMD:C_0805
C32 | 470n | 10V | - | Murata | GRM21BR71H474KA88L | 50V X7R 10% | ~ | Capacitors_SMD:C_0805
C33 | 10μ | 75V | - | Nichicon | UCD1K100MCL1GS | alum. Electrolytic, 80V 20% | ~ | Capacitors_SMD:c_elec_6.3x7.7
C34 | 0.1μ | 10V | - | Murata | GRM21BR71E104KA01L | 25V X7R 10% | ~ | Capacitors_SMD:C_0805
C35 | 10μ | 75V | - | Nichicon | UCD1K100MCL1GS | alum. Electrolytic, 80V 20% | ~ | Capacitors_SMD:c_elec_6.3x7.7
C36 | 150μ | 75V | - | Nichicon | UPW2A151MHD | alum. Electrolytic, 100V 20% | ~ | Capacitors_ThroughHole:C_Radial_D12.5_L25_P5
C37 | 0.1μ | 75V X7R | ceramic | Murata | GRM21BR71H104KA01L | 50V X7R 5% | ~ | Capacitors_SMD:C_0805
D1 | CMMR1U-02 | - | - | Central Semi | CMMR1U-02 TR | - | https://github.com/psas/launch-tower/blob/master/ltc3/doc/datasheets/semiconductors/Central_Semi-CMMR1U_Series-Ultra_Fast_SMT_Rectifier.pdf | Diodes_SMD:SOD-123
D2 | CMMR1U-02 | - | - | Central Semi | CMMR1U-02 TR | - | https://github.com/psas/launch-tower/blob/master/ltc3/doc/datasheets/semiconductors/Central_Semi-CMMR1U_Series-Ultra_Fast_SMT_Rectifier.pdf | Diodes_SMD:SOD-123
D3 | GREEN | - | STATUS | Lite-On | LTST-C150GKT | - | https://github.com/psas/launch-tower/blob/master/ltc3/doc/datasheets/indicators/Lite_On-LTST_C150CKT-LED_Red_1206.pdf | LEDs:LED_1206
D4 | RED | - | FAULT | Lite-On | LTST-C150CKT | - | https://github.com/psas/launch-tower/blob/master/ltc3/doc/datasheets/indicators/Lite_On-LTST_C150GKT-LED_Green_1206.pdf | LEDs:LED_1206
D5 | BZT52C13 | - | 13V | Diodes Inc. | BZT52C13-7-F | - | https://github.com/psas/launch-tower/blob/master/ltc3/doc/datasheets/semiconductors/Diodes_Inc-BZT52C13-Surface_Mount_Zener_Diode.pdf | Diodes_SMD:SOD-123
F1 | 15A | - | - | Keystone | 3557-2 | - | https://github.com/psas/launch-tower/blob/master/ltc3/doc/datasheets/fuses/Keystone-3557_2-automotive_fuse_holder_vertical.pdf | LTC3:Fuseholder_Auto_Blade_Regular_Keystone_3557-2
L1 | 10uH | - | - | Coilcraft | SER2915L-103KL | - | https://github.com/psas/launch-tower/blob/master/ltc3/doc/datasheets/passives/Coilcraft-SER2900-Shielded_Power_Inductors.pdf | LTC3:Coilcraft_SER2900
P1 | MicroFit header | - | DC_IN | Molex | 43045-0828 | 8 pos vertical header | https://github.com/psas/launch-tower/blob/master/ltc3/doc/datasheets/connectors/Molex-43045-Micro_Fit_3_dual_row_vertical_through_hole_header.pdf | Connectors_Molex:Molex_Microfit3_Header_02x04_Straight_43045-0828
P2 | MicroFit header | - | DC_OUT | Molex | 43045-0428 | 4 pos vertical header | https://github.com/psas/launch-tower/blob/master/ltc3/doc/datasheets/connectors/Molex-43045-Micro_Fit_3_dual_row_vertical_through_hole_header.pdf | Connectors_Molex:Molex_Microfit3_Header_02x02_Straight_43045-0428
P3 | XH header | - | to thermistor | JST | B2B-XH-A(LF)(SN) | 2 pos vertical header | https://github.com/psas/launch-tower/blob/master/ltc3/doc/datasheets/connectors/JST-XH-2.5mm_pitch_Disconnectable_Crimp_style_connectors.pdf | Connectors_JST:JST_XH_B02B-XH-A_02x2.50mm_Straight
P4 | MicroFit header | - | to cell protection | Molex | 43045-0228 | 2 pos vertical header | https://github.com/psas/launch-tower/blob/master/ltc3/doc/datasheets/connectors/Molex-43045-Micro_Fit_3_dual_row_vertical_through_hole_header.pdf | Connectors_Molex:Molex_Microfit3_Header_02x01_Straight_43045-0228
P5 | XH header | - | to LTC | JST | B2B-XH-A(LF)(SN) | 2 pos vertical header | https://github.com/psas/launch-tower/blob/master/ltc3/doc/datasheets/connectors/JST-XH-2.5mm_pitch_Disconnectable_Crimp_style_connectors.pdf | Connectors_JST:JST_EH_B02B-XH-A_02x2.50mm_Straight
P6 | XH header |  | to LTC | JST | B4B-XH-A(LF)(SN) | 4 pos vertical header | https://github.com/psas/launch-tower/blob/master/ltc3/doc/datasheets/connectors/JST-XH-2.5mm_pitch_Disconnectable_Crimp_style_connectors.pdf | Connectors_JST:JST_EH_B04B-XH-A_04x2.50mm_Straight
Q1 | ZVN4525E6 | - | - | Diodes, Inc. | ZVN4525E6TA | - | https://github.com/psas/launch-tower/blob/master/ltc3/doc/datasheets/semiconductors/Diodes_Inc-ZVN4525E6-250V_N_Channel_Enhancement_Mode_MOSFET.pdf | LTC3:SOT-26
Q2 | BSC028N06NS | - | - | Infineon | BSC028N06NS | - | https://github.com/psas/launch-tower/blob/master/ltc3/doc/datasheets/semiconductors/Infineon-BSC028N06NS-OptiMOS_Power_Transistor.pdf | Power_Integrations:SO-8
Q3 | BSC028N06NS | - | - | Infineon | BSC028N06NS | - | https://github.com/psas/launch-tower/blob/master/ltc3/doc/datasheets/semiconductors/Infineon-BSC028N06NS-OptiMOS_Power_Transistor.pdf | Power_Integrations:SO-8
Q4 | BSC028N06NS | - | - | Infineon | BSC028N06NS | - | https://github.com/psas/launch-tower/blob/master/ltc3/doc/datasheets/semiconductors/Infineon-BSC028N06NS-OptiMOS_Power_Transistor.pdf | Power_Integrations:SO-8
Q5 | BSC028N06NS | - | - | Infineon | BSC028N06NS | - | https://github.com/psas/launch-tower/blob/master/ltc3/doc/datasheets/semiconductors/Infineon-BSC028N06NS-OptiMOS_Power_Transistor.pdf | Power_Integrations:SO-8
Q6 | ZVP3310F | - | - | Diodes Inc. | ZVP3310FTA | - | https://github.com/psas/launch-tower/blob/master/ltc3/doc/datasheets/semiconductors/Diodes_Inc-ZVP3310FTA-P_Channel_Enhancement_Mode_Vertical_DMOS_FET.pdf | TO_SOT_Packages_SMD:SOT-23
Q7 | MMBT5550L | - | - | ON Semi | MMBT5550LT1G | - | https://github.com/psas/launch-tower/blob/master/ltc3/doc/datasheets/semiconductors/ON_Semi-MMBT5550LT1G-High_Voltage_NPN_BJT.pdf | TO_SOT_Packages_SMD:SOT-23
R1 | 110k | 1% | - | Yageo | RC0805FR-07110KL | - | ~ | Resistors_SMD:R_0805
R2 | 35.7k | 1% | - | Yageo | RC0805FR-0735K7L | - | ~ | Resistors_SMD:R_0805
R3 | 10k | - | - | Yageo | RC0805FR-0710KL | 1% 1/8W | ~ | Resistors_SMD:R_0805
R4 | 10k | - | - | Yageo | RC0805FR-0710KL | 1% 1/8W | ~ | Resistors_SMD:R_0805
R5 | 0 | - | - | Yageo | RC0805JR-070RL | 1/8W | ~ | Resistors_SMD:R_0805
R6 | 0 | - | - | Yageo | RC0805JR-070RL | 1/8W | ~ | Resistors_SMD:R_0805
R7 | 93.1k | - | - | Yageo | RC0805FR-0793K1L | - | ~ | Resistors_SMD:R_0805
R8 | 7.68k | - | - | Yageo | RC0805FR-077K68L | - | ~ | Resistors_SMD:R_0805
R9 | 196k | 1% | - | Yageo | RC0805FR-07196KL | - | ~ | Resistors_SMD:R_0805
R10 | 8.06k | 1% | - | Rohm | MCR10EZHF8061 | - | ~ | Resistors_SMD:R_0805
R11 | 16.5k | - | - | Yageo | RC0805FR-0716K5L | - | ~ | Resistors_SMD:R_0805
R12 | 3.32k | - | - | Yageo | RC0805FR-073K32L | - | ~ | Resistors_SMD:R_0805
R13 | 215k | - | - | Yageo | RC0805FR-07215KL | - | ~ | Resistors_SMD:R_0805
R14 | 21k | - | - | Yageo | RC0805FR-0721KL | - | ~ | Resistors_SMD:R_0805
R15 | 0 | - | - | Yageo | RC0603JR-070RL | - | ~ | Resistors_SMD:R_0603
R16 | 25.5k | - | - | Vishay | CRCW080527K1FKTA | - | ~ | Resistors_SMD:R_0805
R17 | 3.01k | - | - | Yageo | RC0805FR-073K01L | - | ~ | Resistors_SMD:R_0805
R18 | 243k | - | - | Yageo | RC0805FR-07243KL | - | ~ | Resistors_SMD:R_0805
R19 | 10k | - | - | Yageo | RC0805FR-0710KL | 1% 1/8W | ~ | Resistors_SMD:R_0805
R20 | 10m | 1% 1W | - | Vishay | WSLP1206R0100FEA | 1% 1W | ~ | Resistors_SMD:R_1206
R21 | 10 | - | - | Yageo | RC0805FR-0710RL | - | ~ | Resistors_SMD:R_0805
R22 | 53.6k | - | - | Yageo | RC0805FR-0753K6L | - | ~ | Resistors_SMD:R_0805
R23 | 549 | - | RDSA | Yageo | RC0805FR-07549RL | - | ~ | Resistors_SMD:R_0805
R24 | 549 | - | RDFA | Yageo | RC0805FR-07549RL | - | ~ | Resistors_SMD:R_0805
R25 | 0 | - | - | Yageo | RC0603JR-070RL | - | ~ | Resistors_SMD:R_0603
R26 | 1.3k | - | RDSB | Yageo | RC0805FR-071K3L | - | ~ | Resistors_SMD:R_0805
R27 | 3.32k | - | RDFB | Yageo | RC0805FR-073K32L | - | ~ | Resistors_SMD:R_0805
R28 | 10 | - | - | Yageo | RC0805FR-0710RL | - | ~ | Resistors_SMD:R_0805
R29 | 10 | - | - | Yageo | RC0805FR-0710RL | - | ~ | Resistors_SMD:R_0805
R30 | 200k | - | - | Yageo | RC0805FR-07200KL | - | ~ | Resistors_SMD:R_0805
R31 | 5m | 1% 1/8W | - | Vishay | WSL12065L000FEA | 1% 1/4W | ~ | Resistors_SMD:R_1206
R32 | 11.5k | - | - | Yageo | RC0805FR-0711K5L | - | ~ | Resistors_SMD:R_0805
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

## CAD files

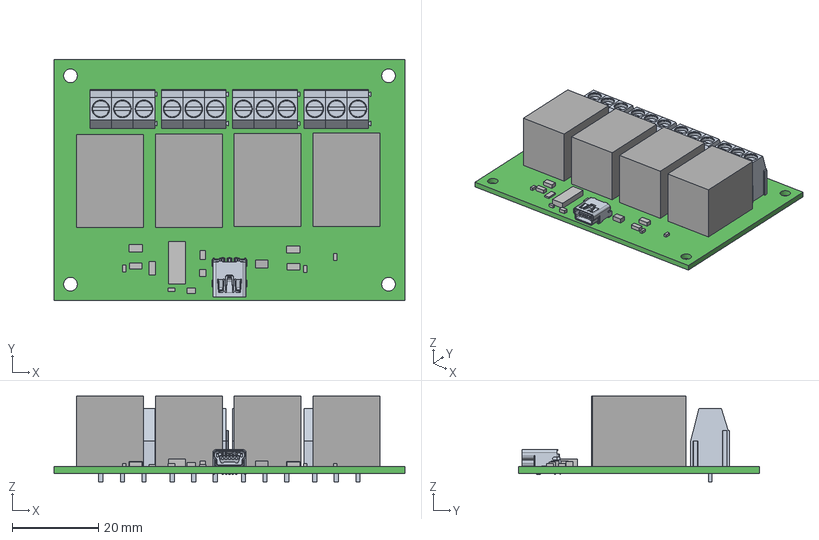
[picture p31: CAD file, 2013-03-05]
eagle/Phidgets - CAD Files/1014_2.step
81.3 x 55.9 x 19.8 mm
Board
Extruded x 18
20020316-G-LEM x 4
20020316-G-CM x 4
20020316-G-REM x 4

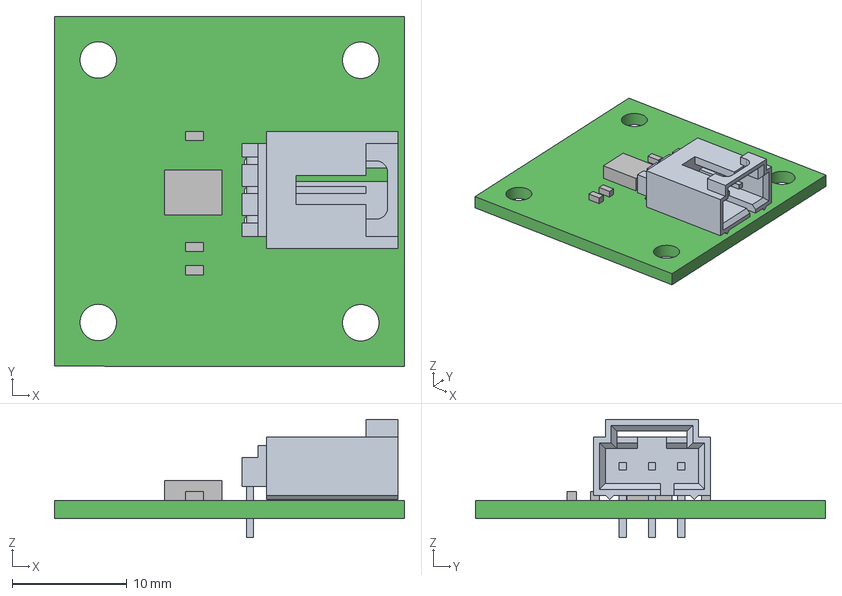
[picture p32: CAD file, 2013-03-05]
eagle/Phidgets - CAD Files/1124_0.step
30.5 x 30.5 x 10.3 mm
Board
Extruded x 4

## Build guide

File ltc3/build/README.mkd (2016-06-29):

# Compiled Objects

Items in this sub-directory have been generated from other source
materials.  Where the objects here diverge from their source materials,
their source materials should be considered authoritative.

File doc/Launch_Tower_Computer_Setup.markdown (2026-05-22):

# Setup the Launch Tower Computer

## BeagleBone Black
 1. Download [beagleboard imager](https://www.beagleboard.org/bb-imager)
 2. Use the imager to flash a microsd card with your image of choice
 3. Insert the microsd into the beaglebone and power it up
 4. Place card in the unpowered BeagleBoard.
 5. Hold down the "User Boot" button, it is the button near the SD card end of the board.
 6. Keep holding down the button and apply power.
 7. Keep holding down the button until the bank of 4 LED's light up for a few seconds. You may now release the button
 8. The system will boot into Debian while the OS is copied onto the eMMC.
 9. When it finishes, the 4 LED's will light up and then it should power itself off.
 10. Remove the SD card and power it up.

## System Setup
 1. Update the package list `apt-get update`
 2. Install all updates. `apt-get upgrade`
 3. Update password to the PSAS standard with `passwd`
 4. Install the [phidgets](https://www.phidgets.com/docs/Phidget22admin_Guide) library and webservice
 5. Check that [launch-tower-comm](https://github.com/psas/launch-tower-comm) runs and connects without errors using the prefconfigured usb network on the bbb

## Configure Systemd Networkd

[Systemd Networkd](https://man7.org/linux/man-pages/man8/systemd-networkd.8.html)

 1. Create a link file to give a persistent name to the network interface

 eg. /etc/systemd/network/10-wifi-dongle.link

 ```
 [Match]
 MACAddress=8c:ef:d5:f6:6a:80

 [Link]
 Name=wlan_dongle
 ```
 Use the actual MACAddress of the wifi dongle you plan to use

 2. Edit /etc/network/interfaces.d/10-wlan-dongle.conf (create this file first)

 ```
 iface wlan_dongle inet static
         hostapd /etc/hostapd/hostapd.conf
 ```

 This will tell systemd to give this interface a static ip address, and let hostapd control it.

## Configure Hostapd

[hostapd](https://manpages.debian.org/testing/hostapd/hostapd.8.en.html)

 1. Edit /etc/hostapd/hostapd.conf

 ```
 interface=wlan_dongle

 # a simply means 5GHz
 # g simply means 2.4GHz band
 hw_mode=g

 # the channel to use
 channel=11

 # limit the frequencies used to those allowed in the country
 #ieee80211d=1
 # the country code
 #country_code=US

 # 802.11n support
 ieee80211n=1
 # QoS support, also required for full speed on 802.11n/ac/ax
 wmm_enabled=1

 ssid=psas-tower-link

 # 1=wpa, 2=wep, 3=both
 auth_algs=1
 wpa=2
 wpa_key_mgmt=WPA-PSK
 wpa_pairwise=TKIP
 rsn_pairwise=CCMP
 wpa_passphrase=psasrocket

 macaddr_acl=0
 ignore_broadcast_ssid=0

 logger_syslog=-1
 logger_syslog_level=2
 ```

This configures the network interface and sets its ssid and passkey

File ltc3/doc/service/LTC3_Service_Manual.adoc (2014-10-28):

= PSAS Launch Tower Computer III Service Manual

Some day, this document will contain service instructions for LTC 3.
But not yet.  We're not finished with the new design yet.

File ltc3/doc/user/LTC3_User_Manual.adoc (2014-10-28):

= PSAS Launch Tower Computer III User Manual

Some day, this document will contain usage instructions for LTC III.
But not yet.  We're not finished with the new design yet.

Much of this document may well end up integrated with the
https://github.com/psas/procedure-book[Procedure Book].

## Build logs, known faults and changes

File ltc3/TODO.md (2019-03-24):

# LTC3 Master To-Do List

More or less in order of priority.  Many tasks can be completed in
parallel.

## Pending

* Finish off-board schematic.  [Paul]

* Update design files and BOMs (parts subsitutions made during board
  assembly; layout errors discovered; etc.)  [Paul]
 
* Figure out how to replace PI2127 ideal diodes on charge controller
  with an off-board switch and mod wires.  [Andy]
  * Update schematic.

* Assemble LTC3 board.  [Andy]

* Buy a battery with a connector that gives us access between each of
  the cells.  OR  Shop for custom battery.  [Paul]

* Shop for remaining parts (mostly off-board, e.g. switches,
  connectors, etc.).  [Paul]

* Finish design documentation (it should at least match the existing
  design).

* Devise a test plan for each board.

* Simulate charge controller.  [Andy]

* Shop for an enclosure.  [Paul]

* Bring up Linux on the BeagleBone.  [Paul]

* Create some proof-of-concept software that can at least twiddle the
  various GPIOs, relays, etc.  [Paul]

## Done

* Tag commit that contains the design files (and Gerbers) from which
  the rev 1 boards were made.  [Paul]
* Fix air-trace on LTC board layout.  [Paul]

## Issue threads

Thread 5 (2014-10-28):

Investigate BeagleBone Black WiFi options

nellump, 2014-10-28:
It would be nice to not have a USB-based WiFi dongle strapped to the inside of the LTC enclosure.  Find out what WiFi adapter options are currently available for the BeagleBone Black.  If there are no existing WiFi capes, perhaps we could integrate a WiFi adapter into our new board. Will the GPIOs support this?

Closed 2015-01-05.

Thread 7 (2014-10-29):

Investigate Intel Edison as a board

OutboundFlight, 2014-10-29:
Initially: the Edison is a lot smaller than the BBB, has very low power requirements, and is an x86 rather than ARM. On the other hand, there's very little support and we would need a separate analog input.

One thing that would help with this project is generating a list of what makes for a good LTC.

nellump, 2015-02-02:
Edison looks like a nice board, and it might even be a better match for LTC3 if it wasn't for the lack of Ethernet.  That's a deal-breaker.  (Ethernet over USB is possible.  Not sure what that does to network latency.)

Expanding on aSmig's comparison above:
* Edison has a 500 MHz dual-core Atom proc.; BBB has a 1 GHz ARM A8 proc.
* Edison has 1 GB RAM; BBB has 512 MB.
* Both boards have 4 GB of eMMC.
* Edison has on-board WiFi and Bluetooth LE.
* Edison has no Ethernet.
* Edison compute module only supports 1.8 V IO.
* Both boards have more GPIOs than we'll know what to do with.
* Both boards can be easily mounted onto an appropriately-designed expansion board.
* Edison compute module is a tiny board with no external interfaces but a single Hirose connector.  It will require an expansion/breakout board to be useful.  In that respect, it is very similar to the Qseven boards.
* Edison has an on-board microcontroller external to the main processor.
* Prices appears to be about the same (~$55).

Reference:
* http://hackaday.com/2014/09/10/hands-on-with-the-intel-edison/
* http://www.mouser.com/new/Intel/intel-edison/
* http://www.amazon.com/dp/B00ND1KH10
* https://www.adafruit.com/products/2112

BartMassey, 2015-02-03:
Ethernet over USB is fine for whatever we're going to be doing, IMHO. Nobody puts it in anymore because that.

Closed 2015-03-23.

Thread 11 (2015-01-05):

inv LTC3 front panel voltmeters

nellump, 2015-01-05:
Need several small, low-power digital voltmeters to provide at-a-glance measurements of the LTC's power rails.

nellump, 2015-02-02:
Discarding this idea.

Closed 2015-02-02.

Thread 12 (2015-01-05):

create diagram of LTC3 power system

nellump, 2015-01-05:
Not a schematic, just a simple, high-level diagram of how the LTC's power sources and supplies relate.

For the purposes of this discussion, "sources" are what provide the LTC3 with its juice; "supplies" are the converted/conditioned power it provides to its subsystems.

nellump, 2015-02-10:
Rough draft committed to ltc3/design/doc/.  More to come.

nellump, 2015-07-01:
Deleted the rough draft.  A standalone diagram is redundant of the top-level KiCad schematic.

Closed 2015-07-01.

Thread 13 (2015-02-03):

select LTC3 12-to-19 V DC-to-DC converter

nellump, 2015-02-03:
This converter will supply the rocket's shore power connection; 19 VDC @ ~ 4 A.

See *Requirements* doc for details.  If you discover additional requirements that are not already in the doc, please update it.

Start off by coming up with a list of promising candidates.  At this point, we will consider both board- and chassis-mount styles.

austinjoseph, 2015-02-13:
**This looked the most promising for a board mounted option, designed to run at constatn 3A out, not quite 4 but it looks like it might work.:
http://www.amazon.com/3-5-30V-4-0-30V-Booster-Converter-Regulator/dp/B008FLE7PA#productDetails

**Another like the above:
http://www.amazon.com/Converter-3-5-28V-1-25-26V-Adjustable-LM2596S/dp/B008ATU2X8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

**Third option... still only 3A:
http://www.amazon.com/Retailstore-LM2596-Adjustable-Supply-Converter/dp/B009HPB1OI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

**This would require a bit of customizing but it has the right input -1 amp on the output but can put out 19V:
http://www.powerstream.com/Produz10.htm

**A comparison of similar converters:
http://www.powerstream.com/ADC-p006.htm

Finding no shortage of 10v to 20v but can't seem to find anything for 12v.
**Here is a 3 amp board mounted dip 10V to 12v DCDC converter:
http://www.globalspec.com/specsearch/partspecs?partId={3438B3BA-DC8B-4446-B89C-F950C086231E}&comp=3660&vid=125098&sqid=11131756

nellump, 2015-02-13:
China via eBay:
* "Waterproof 76W DC-DC Converter DC 12V to19V 4A Boost Step-up Car Power Module"
   * http://www.ebay.com/itm/Waterproof-76W-DC-DC-Converter-DC-12V-to19V-4A-Boost-Step-up-Car-Power-Module-/271772377430
   * 12 V in, 19 V @ 4 A out
   * Waterproof!!!!11
   * ~$13 shipped.

andrewgreenberg, 2015-03-30:
I *love* this last one. Sure, it's not PCB mounted, but you could mount it to the PCB if you wanted to, and then have some euroterminal blocks to screw it into nearby. Or you could mount it nearby on the case and do the same thing. I'm impressed with this one, especially if we buy 2-3 of them. Efficiency isn't outstanding, but it's rated to operate at industrial temperatures.

nellump, 2015-04-02:
I'll order a couple of those cheap Chinese switchers.  We can dissect them at a meeting to see how they look inside.

Closed 2015-04-11.

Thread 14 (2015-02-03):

select LTC3 12-to-5 V DC-to-DC converter

nellump, 2015-02-03:
This converter will supply the computer, ignition board, and any digital peripherals; 5 ±0.25 VDC @ 2 A max.

See *Requirements* doc for details.  If you discover additional requirements that are not already in the doc, please update it.

Start off by coming up with a list of promising candidates.  At this point, we will consider both board- and chassis-mount styles.

nellump, 2015-02-10:
Using Mouser's search tool, the following were found:

* TDK-Lambda CC-E series
   * 9-18 V input; 5 V, 2 A output
   * PCB mounted (through-hole)
   * ~$26
   * [Datasheet](http://www.mouser.com/ds/2/400/cc-e-524996.pdf)
* Recom REC10 series
   * 9-18 V input; 5 V, 2 A output
   * PCB mounted (through-hole or SMD)
   * ~$35
  * [Datasheet](http://www.mouser.com/ds/2/468/REC10-SRW_DRW_Z_Hx-14642.pdf)
* Cincon EC4BU series
   * 9-18 V input; 5 V, 2 A output
   * PCB mounted (through-hole)
   * ~$33
   * [Datasheet](http://www.mouser.com/ds/2/75/EC4BU-190623.pdf)

What other distinguishing characteristics should we be looking at?

Closed 2015-03-24.

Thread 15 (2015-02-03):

select LTC3 main battery cells

nellump, 2015-02-03:
Rechargeable LiPo cells.  14.4 VDC nominal; 4 AH.  See *Requirements* doc for details.

Same style as the existing ignition battery cells?

austinjoseph, 2015-02-04:
Finding tons of LiPo packs for 14.8 nom... hard to find datasheets.  Most of the 4-4.5 mAh run about $50-60.

-Multistar 4mAh 14.8v 4cell (at $24.58, it's the cheapest but still not in the 14.4 range)
 http://www.hobbyking.com/hobbyking/store/__56847__Multistar_High_Capacity_4S_4000mAh_Multi_Rotor_Lipo_Pack.html

-List of Lipo's
http://www.radicalrc.com/category/Lipos-3701--Up-539

-Informative website about LiPo
http://www.aircraft-japan.com/en/datasheet/polyquestxp.htm

nellump, 2015-04-11:
We really ought to perform a power survey of the LTC3 design in  order to determine a suitable battery capacity.  We need to consider the current coming in from the solar cells and/or lab power; the current consumption of all the major LTC3 components (BeagleBone, DC-DC converters, etc.); and the current consumed by any external devices.  Then we need to decide how long we want the battery to last given average and worst case load scenarios.

austinjoseph, 2015-04-18:
We researched the total theoretical worst case scenario power consumption based on the following:

Research:
	Maximum amount of time for battery draw on LTC lipos.
        Minumum amount of current provided.

To calculate the power requirements on the batteries
we specifically needed to calculate

power draw of shore power, BBB, sensors triggers on board.

Shore is 76 Watts
BeagleBone 5 Watts
Converters Worst case efficiency 70%  @  ? Watts
    *   12-5DC      7.14 Watts
    *   12-19DC	    27.14

115.28 Watts @ 14.4 V = ~ 8 amps

Methodology:

input power * efficiency = output power

All sensors are in the range of 400uA which we think the BBB should be able to handle.
Entire switching negligible as well (in the order of mWatts).

Continues Discharge Current on our Lipo pack will need to be ~8A.
Lipo Packs that can provide that current will be able to last an hour to an hour and a half and will cost roughly $120-150.

As the power consumption we found is twice as much as was expected in the data sheets we would appreciate some feedback on the methodology.

BartMassey, 2015-04-19:
Why is shore power 75W, or 30W for that matter? 10W continuous seems like pretty much the maximum you should ever need here unless I'm missing something major. Pointer to the LTC III document that describes power?

15W * 1.33 / 15V = 1.33A

I think this means that you can use a standard laptop battery ($20) and get several hours.

OutboundFlight, 2015-04-19:
We were just going based on the specs that Andrew gave us, which was 4A max at 19V, which we backed out to 80W total.

nellump, 2015-04-19:
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

The LTC3 requirements call for a shore power supply of 19V at up to
4A.  The original shore power supply in LTC2 was only good for 2A, and
apparently that did not suffice.

--
Paul

aSmig, 2015-04-26:
Regarding shore power pulling more than 10 watts;  The FC alone can pull up to 14 watts.  Add two raspberry Pis, a couple STM32 Olimex boards, WiFi amp & transceiver, GPS board, IMU, RNH, servo... and a beefy battery charger.  It might never add up to 76 watts in nominal usage, but we do brown out on power up with less than 40 watts.  AV4 is embarrassingly not power optimized.  But I don't think low power was one of the design goals for AV4.  We did select an Atom, after all.

~8A @ 14V looks right to me.  14.8V is well within our 16.8V max and can probably be considered as good as 14.4V.

Instead of looking for larger capacity 14V packs, I think we should aim for a common size with a good price point and just stack them.  Also, we might get better DC-DC efficiency if we are switching down to 19V from 29V instead of buck-boosting up from 14V.  This would require some reworking of our DC-DC and PV charging systems.

OutboundFlight, 2015-04-26:
So, I was under the impression that the power requirement for the FC was already at 19V. That's what we heard from Andrew, and it's what's in our design spec.

OutboundFlight, 2015-05-01:
Based on discussion tonight we have a new proposal: use two 4-cell custom built LiPos in series, giving us a main battery voltage 28.8V. The main win from this is that we can use way cheaper DC-DC converters (~$30 instead of $100+) and use the same architecture as the Flight Computer. This allows us to copy the charge distributor board from the FC, and use the same battery architecture, so we can have extra spares lying around.

The part number for the LiPo battery cell we currently use is PL5567100, rated at 3.7V, 4250mAh.

Downconverters:
http://www.mouser.com/ds/2/405/slts228c-128240.pdf
We could use this TI converter for both the 5V and 19V rails.

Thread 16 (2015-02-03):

select LTC3 ignition battery charger

nellump, 2015-02-03:
12 VDC input, direct from PV panels.  Not integral to the LTC main board; chassis-mount only.

See *Requirements* doc for details.  If you discover additional requirements that are not already in the doc, please update it.

roman-ku, 2015-02-13:
The ignition battery charger would probably have to be turned on and off manually. I don't the exact details but probably in the field and only when needed.

LiPo battery chargers aren't cheap but it would be still be wise to spend a little more. At a minimum the LiPo charger should have balancing capabilities. A bonus would be temperature sensing, so LiPo charger can auto turn off when it hits a certain temperature threshold.

One option we could use: [Hobbyking® DC-4S Balance Charger & Cell Checker 30w 2s~4s ](http://www.hobbyking.com/hobbyking/store/uh_viewItem.asp?idProduct=36906)

nellump, 2016-09-14:
Ancient issue; no longer relevant.

Closed 2016-09-14.

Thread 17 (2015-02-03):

Investigate BBB display options

nellump, 2015-02-03:
The LTC3 *Requirements* doc calls for a front panel display to convey various vital signs to the user.  Research what the BeagleBone Black supports, and shop for promising candidates.

See Requirements doc for details. If you discover additional requirements that are not already in the doc, please update it.

austinjoseph, 2015-02-03:
-BeagleBoneBlack Cape ("4.3) LCD, only compatible with BBB... It's a touch screen and pricey at ~$65
     -https://www.sparkfun.com/products/12085
     -http://www.mouser.com/ProductDetail/4D-Systems/4DCAPE-70T/? qs=AAveGqk956GzboWsp1MGLg%3D%3D&kpid=1024863130&gclid=CJy2lre8xsMCFdKEfgodRBMAgw   (This is a 7 inch similar version for $89)

- "4.3 40-pin TFT Display ~$26... also an LCD
     http://www.ebay.com/itm/4-3-034-40-Pin-TFT-Display-480x272-With-Touchscree-n-/201111080157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

austinjoseph, 2015-04-17:
Denistron has a line of outdoor lcd's [here][1] is a link to a typical data sheet.
   *   8.4" diagonal display size
   *   Anti-glare
   *   4 wire resistive touch
   *   "Vandal" resistant film to glass design.

[1]http://www.densitron.com/GetPdf.aspx?nDisplayID=489

nellump, 2016-09-14:
Ancient issue; no longer relevant.

Closed 2016-09-14.

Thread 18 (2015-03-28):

Select Relay Driver Technology for LTC3 External Triggers

nellump, 2015-03-28:
The BeagleBone GPIO have a very limited current sourcing capability, not nearly enough to drive a typical 12V relay.  We'll either need to use discrete driver transistors, one each connected to its own GPIO, or use a relay driver IC (connected to the BBB over I2C or SPI).  Investigate amongst yourselves.  Refer to the Requirements Spec for details, as necessary.

nellump, 2015-03-28:
Linear Technology offers an I2C-based relay driver chip, [LTC4255][1].  Four independent open-collector drivers; short-circuit and over-current (foldback) protection; etc.

[1]: http://cds.linear.com/docs/en/datasheet/4255f.pdf

nellump, 2015-03-28:
Relay-driving capes are also available, including a [four-relay 3 A cape][1] from CircuitCo.

[1]: http://elinux.org/CircuitCo:Relay_Cape

nellump, 2015-03-29:
Possibilities:
* MC33879: Configurable Octal Serial Switch, Open Load Detect
  * http://www.freescale.com/webapp/sps/site/prod_summary.jsp?code=MC33879

BartMassey, 2015-03-30:
What are the relay coil current requirements? Why are we using relays instead of solid-state switches in the first place? Is there really any reason not to just use a MOSFET per GPIO?

nellump, 2015-04-01:
Haven't settled on a specific relay, yet.  IIRC, 30-50 mA is a typical 12 V relay coil current.

Relays seem simpler and more robust to me, but that could be due to lack of experience with MOSFETs.

OutboundFlight, 2015-04-01:
Isn't there also a safety/reliability issue? Because the relays are driving the igniter and RocketReady for the launch system. Are relays considered more reliable than transistors?

BartMassey, 2015-04-01:
Transistors are way more reliable than relays if they are protected properly. Mechanical failure modes are unpredictable, whereas transistor failure modes are highly predictable/repeatable.

Just use a MOSFET directly. If there are unusual voltage or current requirements, use a "solid-state relay" (http://www.digikey.com/product-search/en/relays/solid-state-relays/1048664). If you must use a mechanical relay use a MOSFET for the coil.

nellump, 2015-04-02:
The current implementation is based on your second suggestion (MOSFET driving a mechanical relay's coil).  (This is also Andrew's suggested circuit.)  The MOSFETs are good for several amps, though.  Would we need to worry about heat dissipation if we drove the external triggers directly with MOSFETs?

BartMassey, 2015-04-02:
I doubt it. The effective resistance of the MOSFET is really tiny, so it doesn't really dissipate noticeable power except when switching. Like I say, check out the "solid state relay" chips I referenced earlier: they are basically a FET with some protection circuitry. I think you'll find reasonably-priced things rated for our application.

andrewgreenberg, 2015-04-06:
You have to worry a little bit about thermal dissipation, but only if you choose the wrong one. Here's a [better list](http://www.digikey.com/product-search/en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) for you from Digi-Key. Some of them are absolutely huge, either in area or height, but many of them are simple 8 pin SMT parts.

Here's my favorite huge [ginourmous one](http://www.digikey.com/product-detail/en/CPC1907B/CLA394-ND/3908816).

And my favorite [small one]( http://www.digikey.com/product-detail/en/TLP3542%28F%29/TLP3542F-ND/871299).

I'd go for the small one. You'll still need a small N channel MOSFET to run on the LED of the "solid state relay", but that's OK. And now no bouncing of the contacts :)
 but no clicking noise either :(

We can chat Tuesday, but let's wrap it up then so you can move on.

nellump, 2015-04-09:
Andrew and the LTC3 team conferred at Tuesday's general meeting, and have settled on using MOSFET-driven photorelays for control of external devices' power and triggering.  I will update the design spec accordingly.

Closed 2015-04-09.

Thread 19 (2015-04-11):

Select enclosure for LTC3

nellump, 2015-04-11:
Shop for a new enclosure for LTC3.  The redesign should allow us to use a significantly smaller enclosure than the one used by LTC2.

The requirements doc does not include many specific details about the enclosure.
   * Either heavy duty plastic (like LTC2) or metal would be acceptable.
   * Dust and dirt protection would be a very good idea.
   * Moisture-proof would be nice, but unlikely to ever be a problem in our launch environment.
   * The enclosure-to-tower mounting scheme needs to be sturdy and straightforward (tool-free, preferably).

We'll need to have a good idea of the size of the LTC3 main board prior to making a final selection.

austinjoseph, 2015-04-11:
NEMA Boxes has this enclosure.
   *   Gasketed
   *   Has two doors, the first is clear plexiglass the second is aluminum.
   *   Easy clip for access for possible front LED.
   *   They make an outdoor version that is UV stabilized.
   *   Dim offered are:
     *   11.3X7.5X5.5 (H/W/D rough)
     *   15.7X11.7X6.3 (H/W/D rough)
     *   19.2X14.6X7.9 (H/W/D rough)
   *    http://www.budind.com/images/product/large/nema-boxes-uni-nbe.jpg

austinjoseph, 2015-04-15:
Hammond offers [this enclosure][1] in their "NEMA Boxes" line:
   *   Gasketed
   *   Mild steel has UV protected cutout for LCD
   *   Flanged mounts available.
   *   Dim offered are:
     *   Highly variable.
     *   16X12X6 (H/W/D rough)
        *   Viewing Window:  11.33X6.71(H/W)

[1]: https://www.hammfg.com/electrical/products/industrial/en4sdw

austinjoseph, 2015-04-15:
Hammond also offers [this enclosure][1]:
   *   Gasketed
   *   Mild steel.
   *   Flanged mounts.
   *   Tooled lock
   *   Galvanized removable panel
   *   No front panel for LCD
   *   Dim offered are:
     *   Highly variable.
     *   16X12X6 (H/W/D rough)
        *   Viewing Window:  11.33X6.71(H/W)

[1]: https://www.hammfg.com/electrical/products/industrial/ej

nellump, 2015-04-15:
We'll need to consider how the LTC enclosure will mount to the tower.  Many (most?) of the industrial enclosures we've seen support DIN mounting rails, which are pretty slick.  [Read][1] and [watch][2] all about it.

[1]:http://www.designnews.com/author.asp?section_id=1386&doc_id=224061&print=yes
[2]: https://www.youtube.com/watch?v=MuF49GPcNG4

natronics, 2015-04-15:
How much do these boxes weigh?

austinjoseph, 2015-04-15:
3-16lbs

On Wednesday, April 15, 2015, Nathan Bergey <notifications@github.com>
wrote:

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

dsigma, 2015-04-16:
The current plan is to mount a piece of 0.25" aluminum flat bar across the back of the tower, and you can bolt/drill/screw anything you want to that flat bar. However, we want to avoid things protruding too far from the flat bar so that the sections can lay nicely on the ground and avoid snagging people while moving them.

austinjoseph, 2015-04-16:
They all have or have the option to come from the factory with a flat
angled bar that comes off the top side of the enclosure.

On Wed, Apr 15, 2015 at 5:43 PM, Dave Camarillo <notifications@github.com>
wrote:

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

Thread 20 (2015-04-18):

Create schematic sheet for LTC3 5 V DC-DC converter

nellump, 2015-04-18:
A placeholder sheet ("DC-DC Converter, 5V") already exists.  Drawing up the schematic should be reasonably straightforward.

We're using a Cincon EC4BU-12S05.  Refer to the design spec and data sheet for the particulars.  A custom component will likely need to be drawn to represent the converter.  The data sheet contains a table of pin assignments.

Please *do not* commit your work to the repo's "master" branch.  [Create a new branch.][1]  We can merge to "master" when you're finished.

[1]: http://www.sbf5.com/~cduan/technical/git/git-2.shtml

austinjoseph, 2015-05-30:
USING TI PTN78020A

austinjoseph, 2015-07-24:
Going to start working on this unless Roman comes back anytime soon!

nellump, 2015-07-24:
DC-DC converter schematics are already completed.  I forgot to check the issues list to close off anything applicable.

Closed 2015-07-24.

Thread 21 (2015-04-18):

Create schematic sheet for LTC3 19 V DC-DC converter

nellump, 2015-04-18:
A placeholder sheet ("DC-DC Converter, 19V") already exists. Drawing up the schematic should be reasonably straightforward.

We're using a nameless switching converter shipped direct From China, With Love. Datasheet? [Ha! Ha!][1] The [eBay auction page][2] makes the following claims:
   * Input voltage: 12V (10V-15V)
   * Output voltage: 19V
   * Output Current: 4A
   * Output power: 76W
   * Soft start time: 500mS
   * Over-current protection
   * Overheat protection
   * Short-circuit protection and automatic recovery
   * Full waterproof potting
   * Conversion efficiency: >85%
   * Load regulation: ± 2%
   * Voltage regulation: ±1%
   * Dynamic response speed: 5% 200uS
   * Module Properties: Non-isolated
   * working temperature: industrial grade(-20° C to 85° C)
   * Distance between mounting 2 holes:55mm
   * Diameter of mounting hole: 7mm
   * Size:68*58*25(mm)
   * Weight:160g

[1]: http://vignette3.wikia.nocookie.net/simpsons/images/e/e9/Nelson_Ha-Ha.jpg
[2]: http://www.ebay.com/itm/Waterproof-76W-DC-DC-Converter-DC-12V-to19V-4A-Boost-Step-up-Car-Power-Module-/271772377430

A custom component will likely need to be drawn to represent the converter. From the photos on the auction page, it appears to be a four-terminal device (Vin, 2x ground, Vout).

Please *do not* commit your work to the repo's "master" branch.  [Create a new branch.][3]  We can merge to "master" when you're finished.

[3]: http://www.sbf5.com/~cduan/technical/git/git-2.shtml

austinjoseph, 2015-05-30:
USING TI PTN78020H For high powered rail.

Closed 2015-07-24.

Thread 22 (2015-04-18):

Create schematic sheet for LTC3 power in

nellump, 2015-04-18:
A placeholder sheet ("Power In") already exists. This schematic should contain circuitry related to the solar cell and lab power inputs (connectors, conditioning, etc.).  Refer to the design spec and LTC2 schematics for guidance.

Please do not commit your work to the repo's "master" branch. Create a new branch. We can merge to "master" when you're finished.

austinjoseph, 2015-04-20:
Taking a shot at this.  Are we just going to use pins for the power in?  I'm looking at other options (XLR) because it seems like it would be nice if things were uniform and easily plugged in unplugged.  Thoughts?

nellump, 2015-04-20:
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

Unless we want to mount the connectors directly to the board, and then
deal with mounting the board in the enclosure so that it's flush with
the sides (all of which sounds like extra work), we should probably go
with something generic like Eurostyle connectors on the board, which
can then be wired up to the external connectors mounted on the
enclosure.

nellump, 2016-09-14:
Ancient issue; no longer relevant.

Closed 2016-09-14.

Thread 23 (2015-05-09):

LTC  Power architecture overview - Review switching from 4s to 8s batteries, plus part choices

OutboundFlight, 2015-05-09:
Cross-posted to Avionics list.

I wanted to send out an update about some design decisions the LTC made recently and solicit feedback.

Based on internal discussions and conversations with Andrew and Kenny, we've decided to swtich from a 14.4V nominal, 4s lipo battery to a 28.8V nominal, 8s lipo configuration.

The primary advantage of this is that it lets us use buck converters down to our power rails at 19V and 5V; configurable buck converters are cheap and easy to find, and have higher efficiencies at a low price point than the boost converters.

The downside of this is that we need to do a custom charging circuit because we're moving away from standard 12V nominal MPPT and 4s battery setups.

But, upon further investigation, we found the LT8490, which is a combination charger/voltage regulator/solar MPPT, and is discussed below. It will be difficult to implement but is a big win as far as cost and system flexibility.

PRELIMINARY COMPONENT CHOICES FOR LTC POWER SYSTEMS:
Voltage regulators:
This is a 7-pin drop-in converter. It's about $30 per, but it will just work, and give us the current, power, and temperature specs we need.
TI PTN78020H (19V rail)
TI PTN78020W (5V rail)

Battery front-end:
LT8490
This is a switching buck/boost regulator with a wide input/output range + charging (LiPO compatible) + solar MPPT. It's very robust and costs about $15. This will be the most complicated circuit and largest time investment of our design, but the work will largely transfer over to the CubeSat power systems.

Battery protection:
TI BQ77PL900
This is a cell protector/balancer that normally runs on I2C with an analog front-end, but can be configured for stand-alone operation. It is cheap, relatively simple to use, and will do cell balancing for us in the field.

Battery:
Because we need at least a 2V overhead to provide 19V for shore power in order to use a down-regulator, we will likely use an 8s configuration. 6s is too close (21.6V) to the output, and 7s is available but is a very non-standard battery configuration.
Based on assumptions: 90% efficiency, calc. 96W of power (a conservative estimate), 4 hours pure battery, we need a capacity of:

13.2Ah at 28.8V nominal (8s)
15.2Ah at 25.2V nominal (7s)
17.8Ah at 21.6V nominal (6s)

We can get two 8s packs at 5.8Ah or four 4s packs at 5.8Ah for around $160.
Here's a good option:
http://www.hobbyking.com/hobbyking/store/__21385__ZIPPY_Compact_5800mAh_8S_25C_Lipo_Pack.html

Here's a higher energy-density, lower-discharge (but more than high enough for our purposes) option for the same price:
It's a 4p2s pack with 16Ah of storage.
http://www.hobbyking.com/hobbycity/store/uh_viewItem.asp?idProduct=66309&aff=3019
However, it seems to be perpetually out of stock. We'll keep an eye on it; this would be bulkier but a ton of storage.

OutboundFlight, 2015-06-25:
Given that we seem to be going ahead with this design, I'll close this issue.

AichaPacem, 2016-05-16:
Hi,
Is there any update concerning LT8490 schematics? :)

Closed 2015-06-25.

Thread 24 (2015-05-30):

Make BQ77PL900 footprint and schematic symbol in KiCAD

OutboundFlight, 2015-05-30:

austinjoseph, 2015-05-30:
Component and Module Finished 30 May.

OutboundFlight, 2015-05-30:
We need to vet this footprint against a known-good footrprint for this chip. There's one in the Eagle TI library under "DL R-PDSO-G48."

austinjoseph, 2015-07-22:
The newer build of kicad has a standard footprint for this chip.  The schematics are already in the repo.

Closed 2015-07-22.

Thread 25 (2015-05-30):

Make PTN708020 footprint and schematic symbol in KiCAD

OutboundFlight, 2015-05-30:
Double check if there are any pinout differences between the low- and high-powers versions.

nellump, 2015-05-31:
I've already got a component (schematic symbol) created for the PTN78020W, saved to the LTC3_components.lib library.  It can be copied to create the PTN78020H.  Pretty sure their pin-outs are identical, but do verify.

OutboundFlight, 2015-05-31:
Okay! I didn't catch that. I'll check the pinouts  tonight and then close
the issue.

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

OutboundFlight, 2015-05-31:
Pinouts for both the high- and low-power version are identical. Closed.

Closed 2015-05-31.

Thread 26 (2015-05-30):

Get demo boards for charger, battery protection chips

OutboundFlight, 2015-05-30:

nellump, 2016-09-14:
Ancient issue; no longer relevant.

Closed 2016-09-14.

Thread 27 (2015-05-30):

Document LT8490 configuration options

OutboundFlight, 2015-05-30:

OutboundFlight, 2015-05-31:
./ltc3/doc/design/LTC3_Power_Configuration.adoc  now contains a summary overview of options for LT8490 config. as well as recommendations for configuration for our use case. The only issue that does not seem to have an obvious recommendation is whether we should implement "Remote Battery Voltage Sensing" as shown in the datasheet because this configuration would guard against hot plugging problems, i.e. transient inrush current due to plugging a charged battery or illuminated solar panel into the system.

Closed 2015-05-31.

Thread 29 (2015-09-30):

Find/Create footprint for LTC2991

austinjoseph, 2015-09-30:

nellump, 2015-09-30:
I created both a schematic symbol and PCB footprint for the LTC2991 when I designed a break-out board for it.  They're available in my kicad-libs repo:

Symbols:
   * https://github.com/nellump/kicad-libs/tree/master/symbols
   * Get both LTC299x.dcm and LTC299x.lib

Footprint:
   * https://github.com/nellump/kicad-libs/blob/master/footprints.pretty/MSOP-16.kicad_mod

nellump, 2015-10-01:
The LTC3 schematics already include a pair of LTC2991 ICs.  I've added a copy of the LTC2991.dcm and .lib files I created for the breakout board, so we have our own copy here (in addition to whats in Launch_Tower_Computer_III-cache.lib).

I've also added a copy of the MSOP-16 footprint, so it's there when we're ready for it.

austinjoseph, 2015-10-02:
Ah cool, thanks Paul.  Was just going through stuff and seeing what I could
get done.  The footprint looks great.  We are going to do some
administrative housekeeping today and create/close git issues.  Are you
back in town yet?

On Wed, Sep 30, 2015 at 9:12 PM, Paul Mullen <notifications@github.com>
wrote:

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

Closed 2015-10-01.

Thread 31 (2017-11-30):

Beaglebone black UART0 pin details on p8 and p9 header

vinayashreeks, 2017-11-30:
hi
I am using beaglebone black ,but due to some reasons i am not able to use 6 pin header for serial debug.May i know which pins in p8 and p9 headers corresponds to uart0_tx and uart0_rx.please help me,i know other uarts pin details ,but only uart0 i need.
@vosechu @donpdonp @fitzgen @aperiodic @BartMassey @beagleboneblack @ti @uart @andrewgreenberg @guileschool

andrewgreenberg, 2017-11-30:
Hi vinayashreeks, why in the world are you asking us these questions in the PSAS launch-tower  repository. Please use the issues ONLY for issues regarding the PSAS launch-tower, and NOT for random questions that you have. Please go find an appropriate BeagleBone forum.

Closed 2017-11-30.

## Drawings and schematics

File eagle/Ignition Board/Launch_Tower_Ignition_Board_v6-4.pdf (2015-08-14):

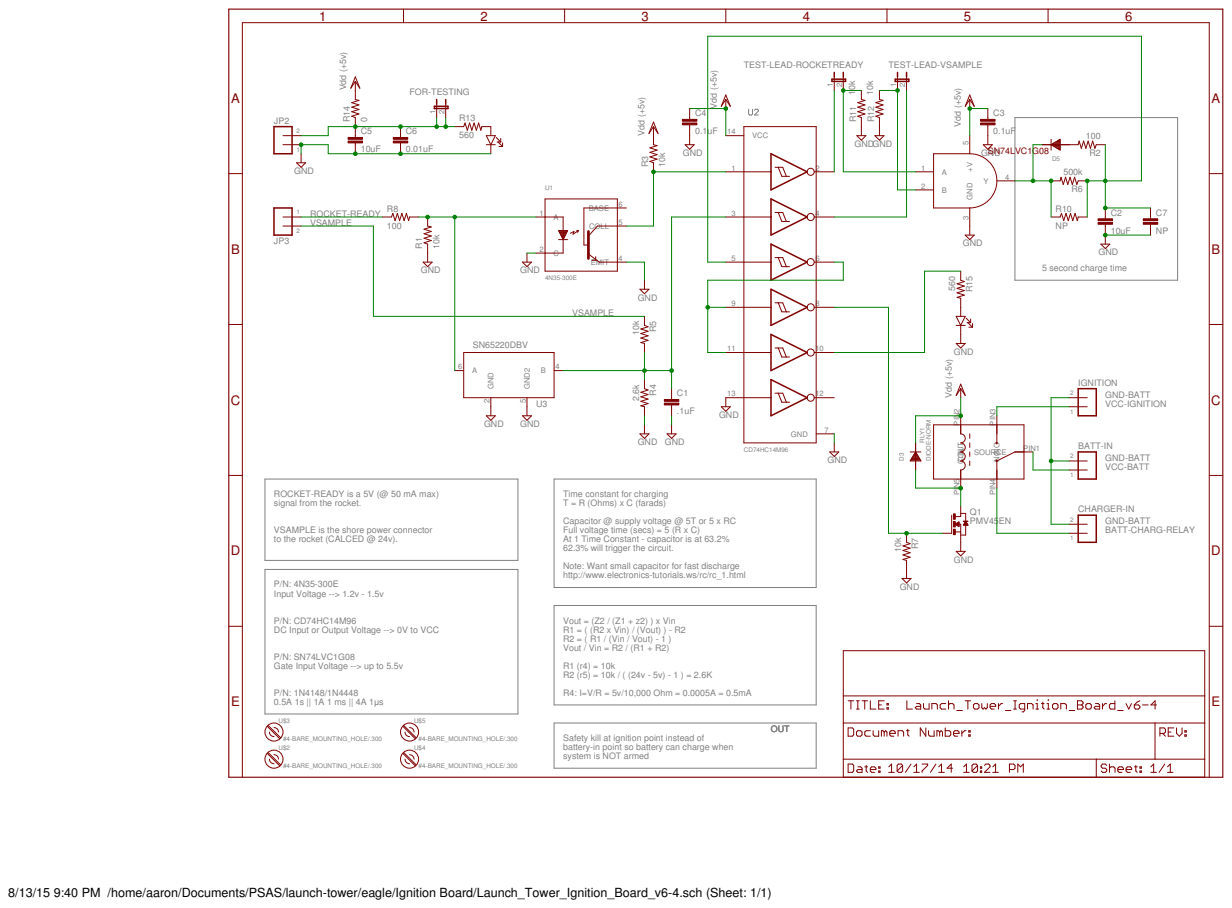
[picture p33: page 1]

9 | GND | 8

ROCKET-READY is a 5V (@ 50 mA max) signal from the rocket. VSAMPLE is the shore power connector

Time constant for charging
T = R (Ohms) x C (farads)
Capacitor @ supply voltage @ 5T or 5 x RC
Full voltage time (secs) = 5 (R x C)
At 1 Time Constant - capacitor is at 63.2%
62.3% will trigger the circuit.
Note: Want small capacitor for fast discharge Vout = (Z2 / (Z1 + z2) ) x Vin R1 = ( (R2 x Vin) / (Vout) ) - R2
http://www.electronics-tutorials.ws/rc/rc_1.html

to the rocket (CALCED @ 24v).

DC Input or Output Voltage --> 0V to VCC

Safety kill at ignition point instead of
battery-in point so battery can charge when
system is NOT armed

8/13/15 9:40 PM /home/aaron/Documents/PSAS/launch-tower/eagle/Ignition Board/Launch_Tower_Ignition_Board_v6-4.sch (Sheet: 1/1)

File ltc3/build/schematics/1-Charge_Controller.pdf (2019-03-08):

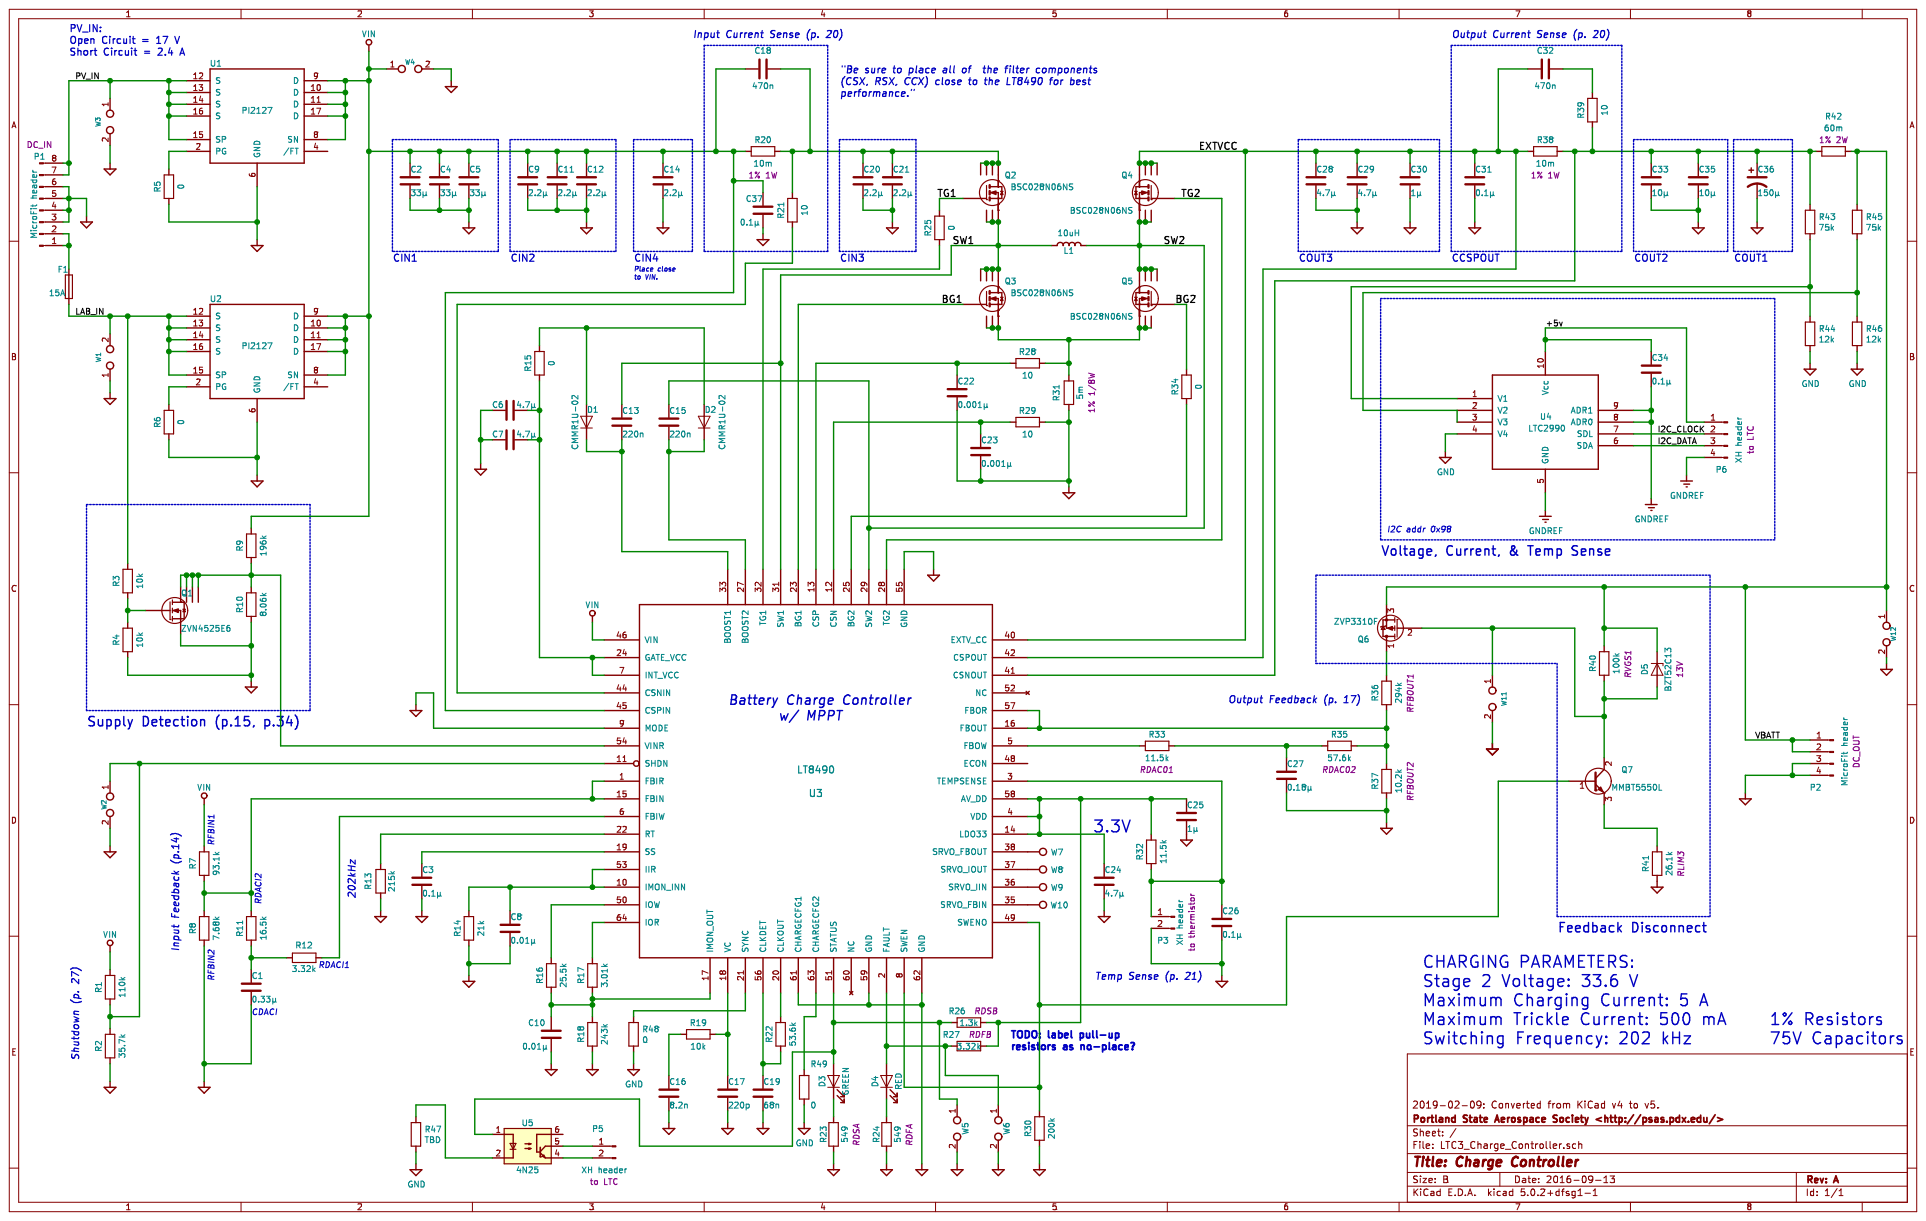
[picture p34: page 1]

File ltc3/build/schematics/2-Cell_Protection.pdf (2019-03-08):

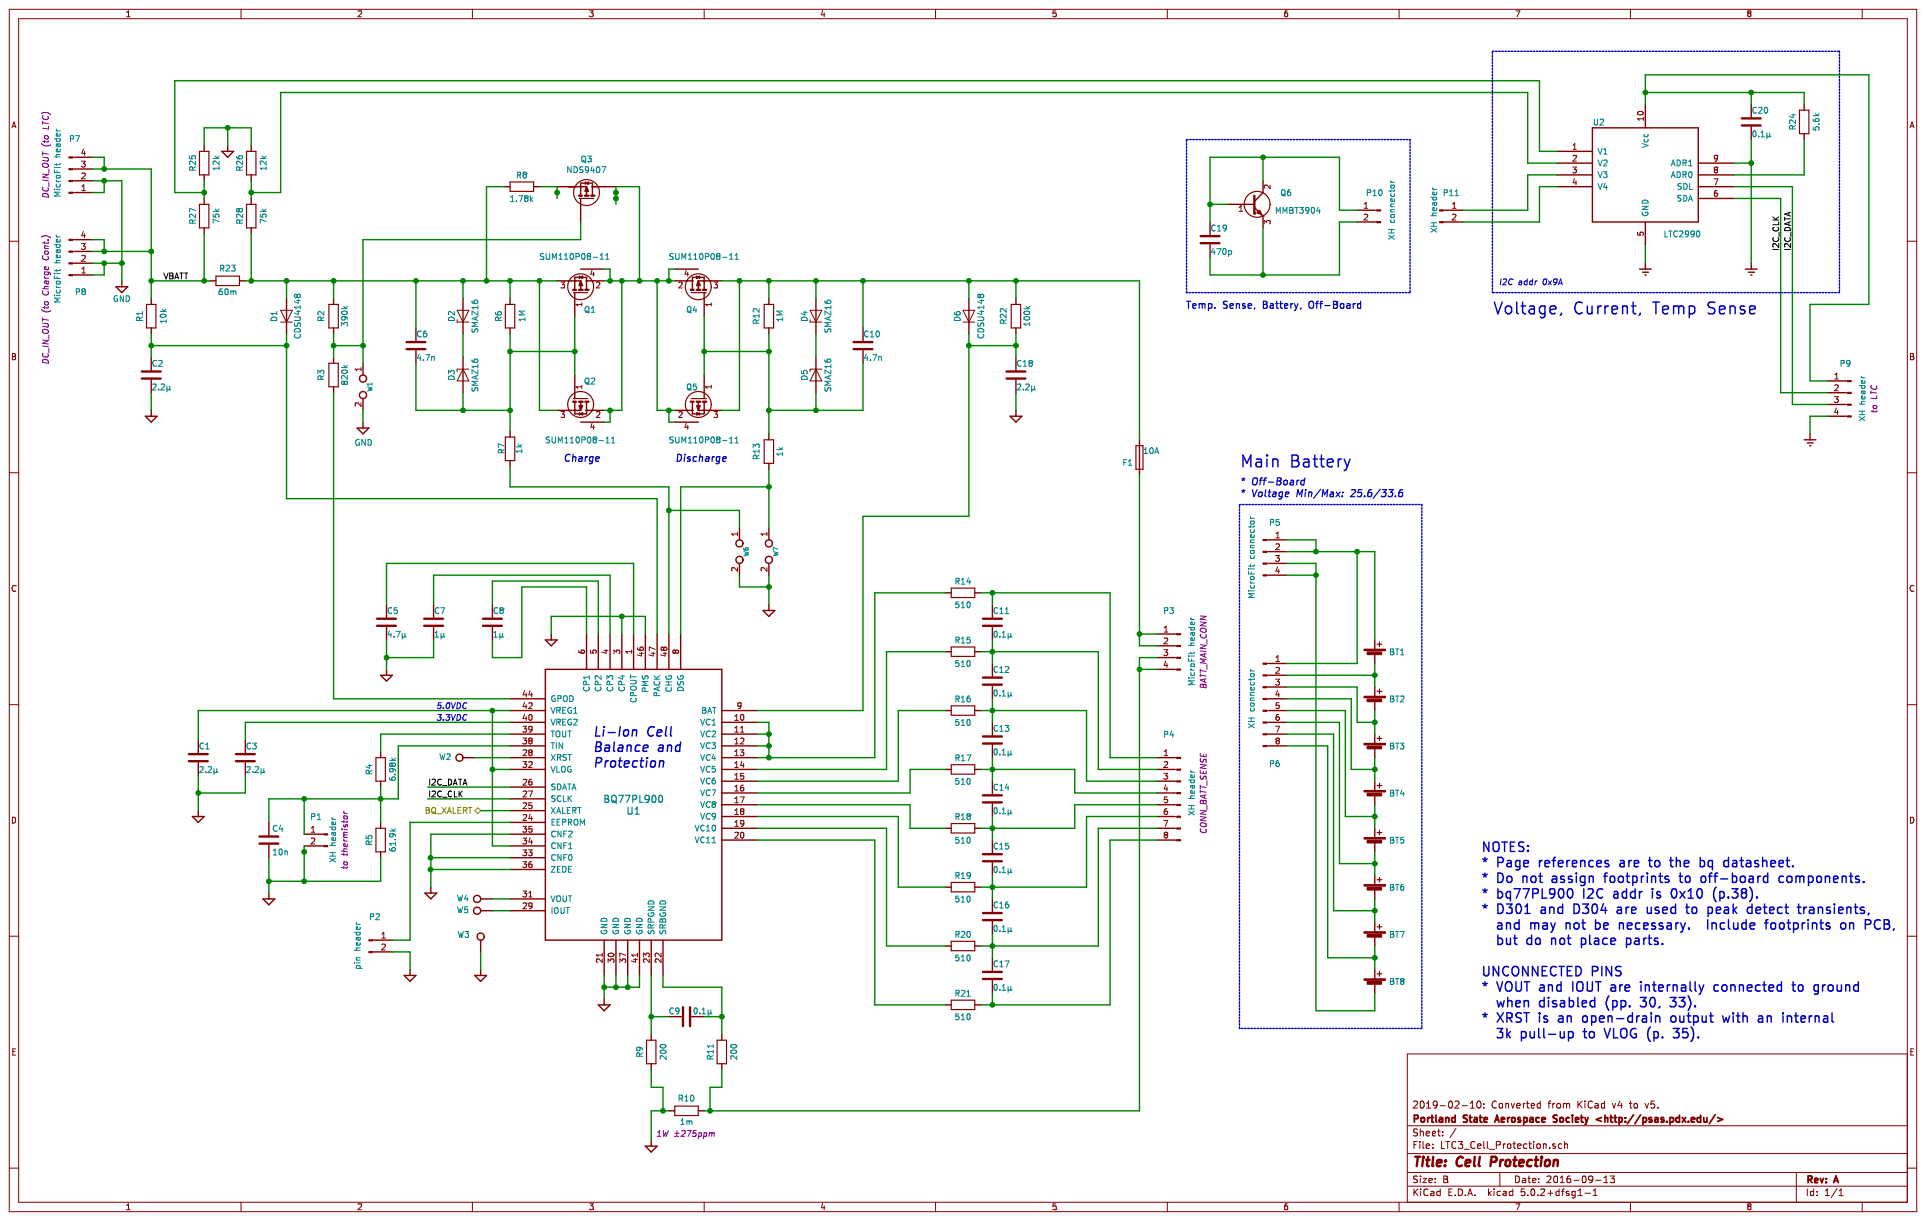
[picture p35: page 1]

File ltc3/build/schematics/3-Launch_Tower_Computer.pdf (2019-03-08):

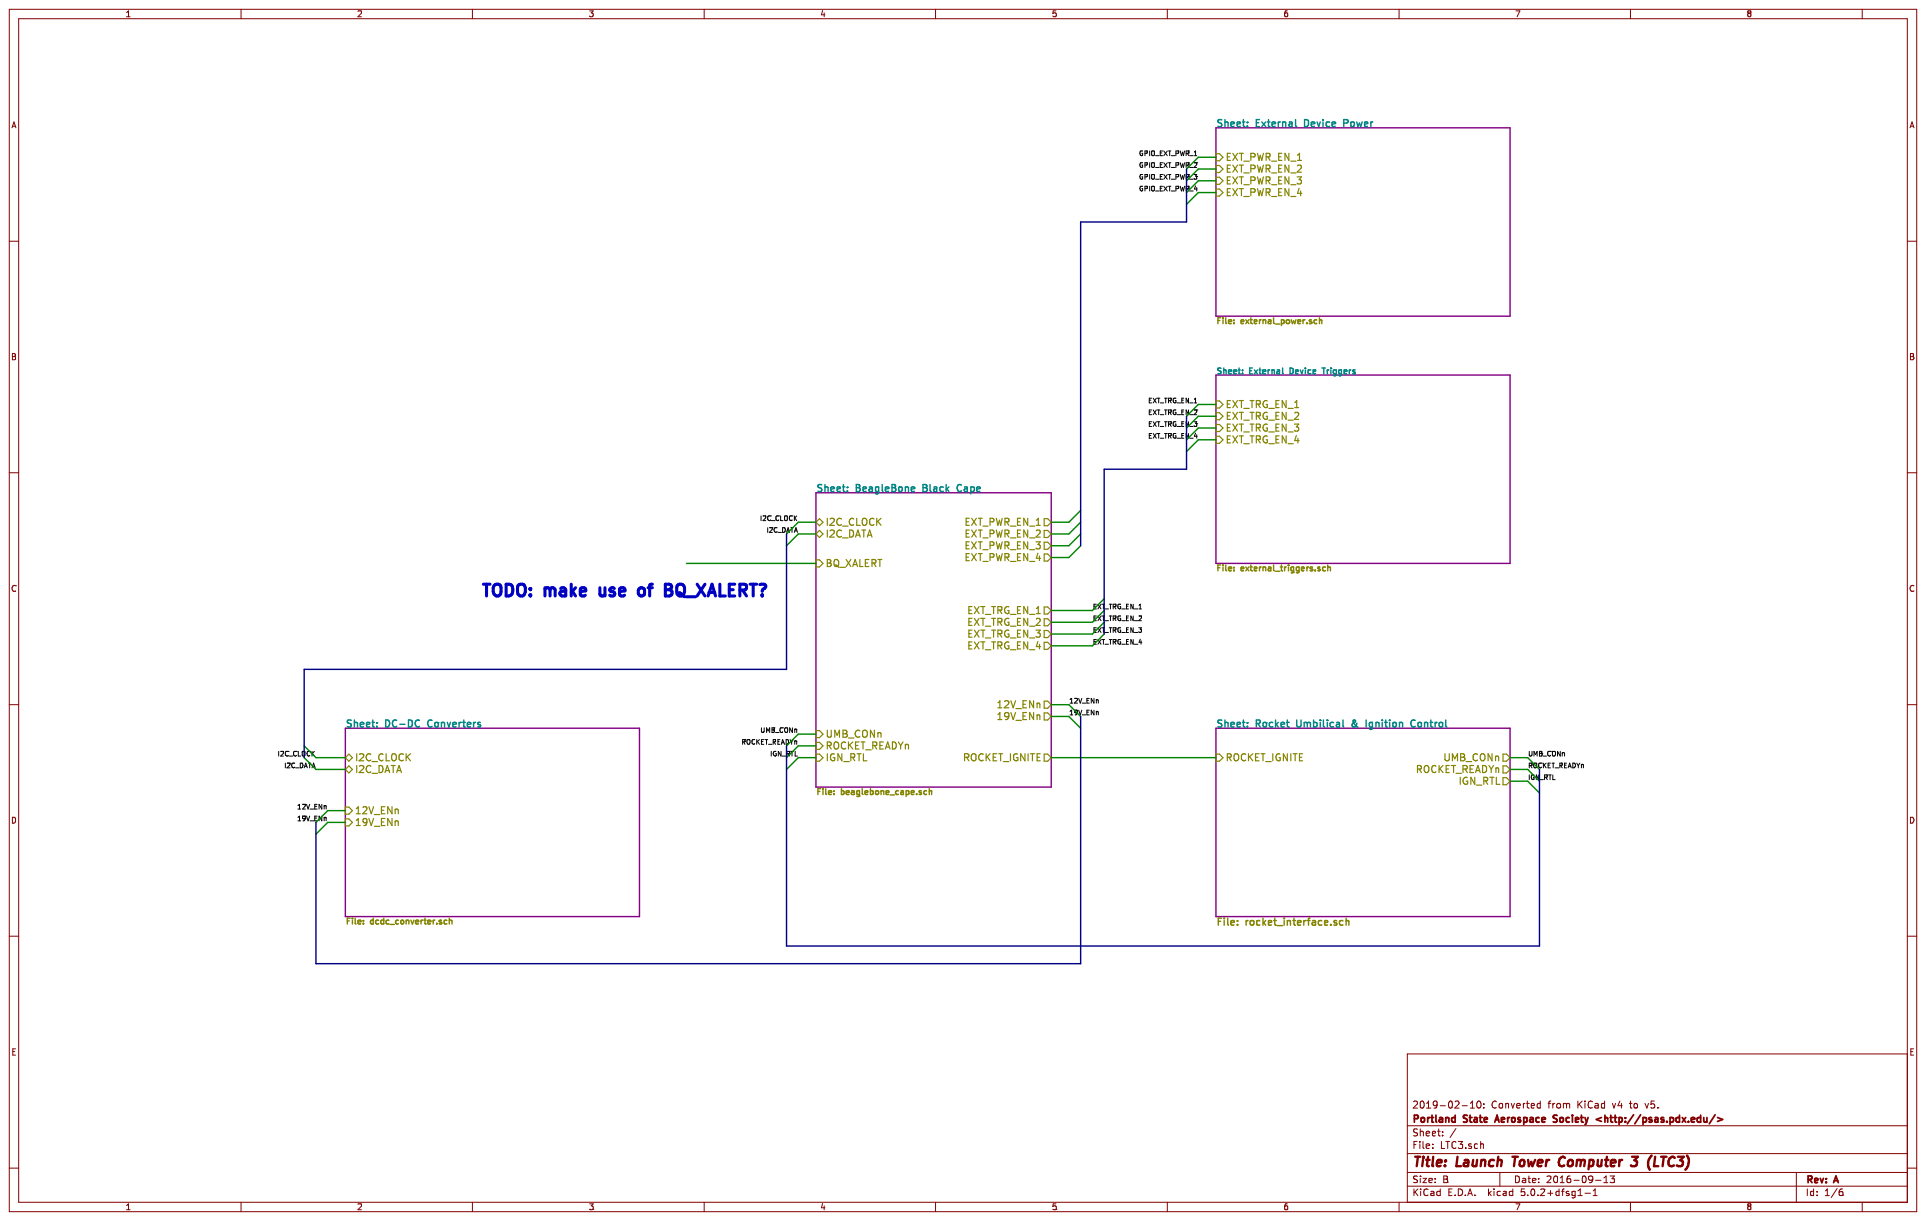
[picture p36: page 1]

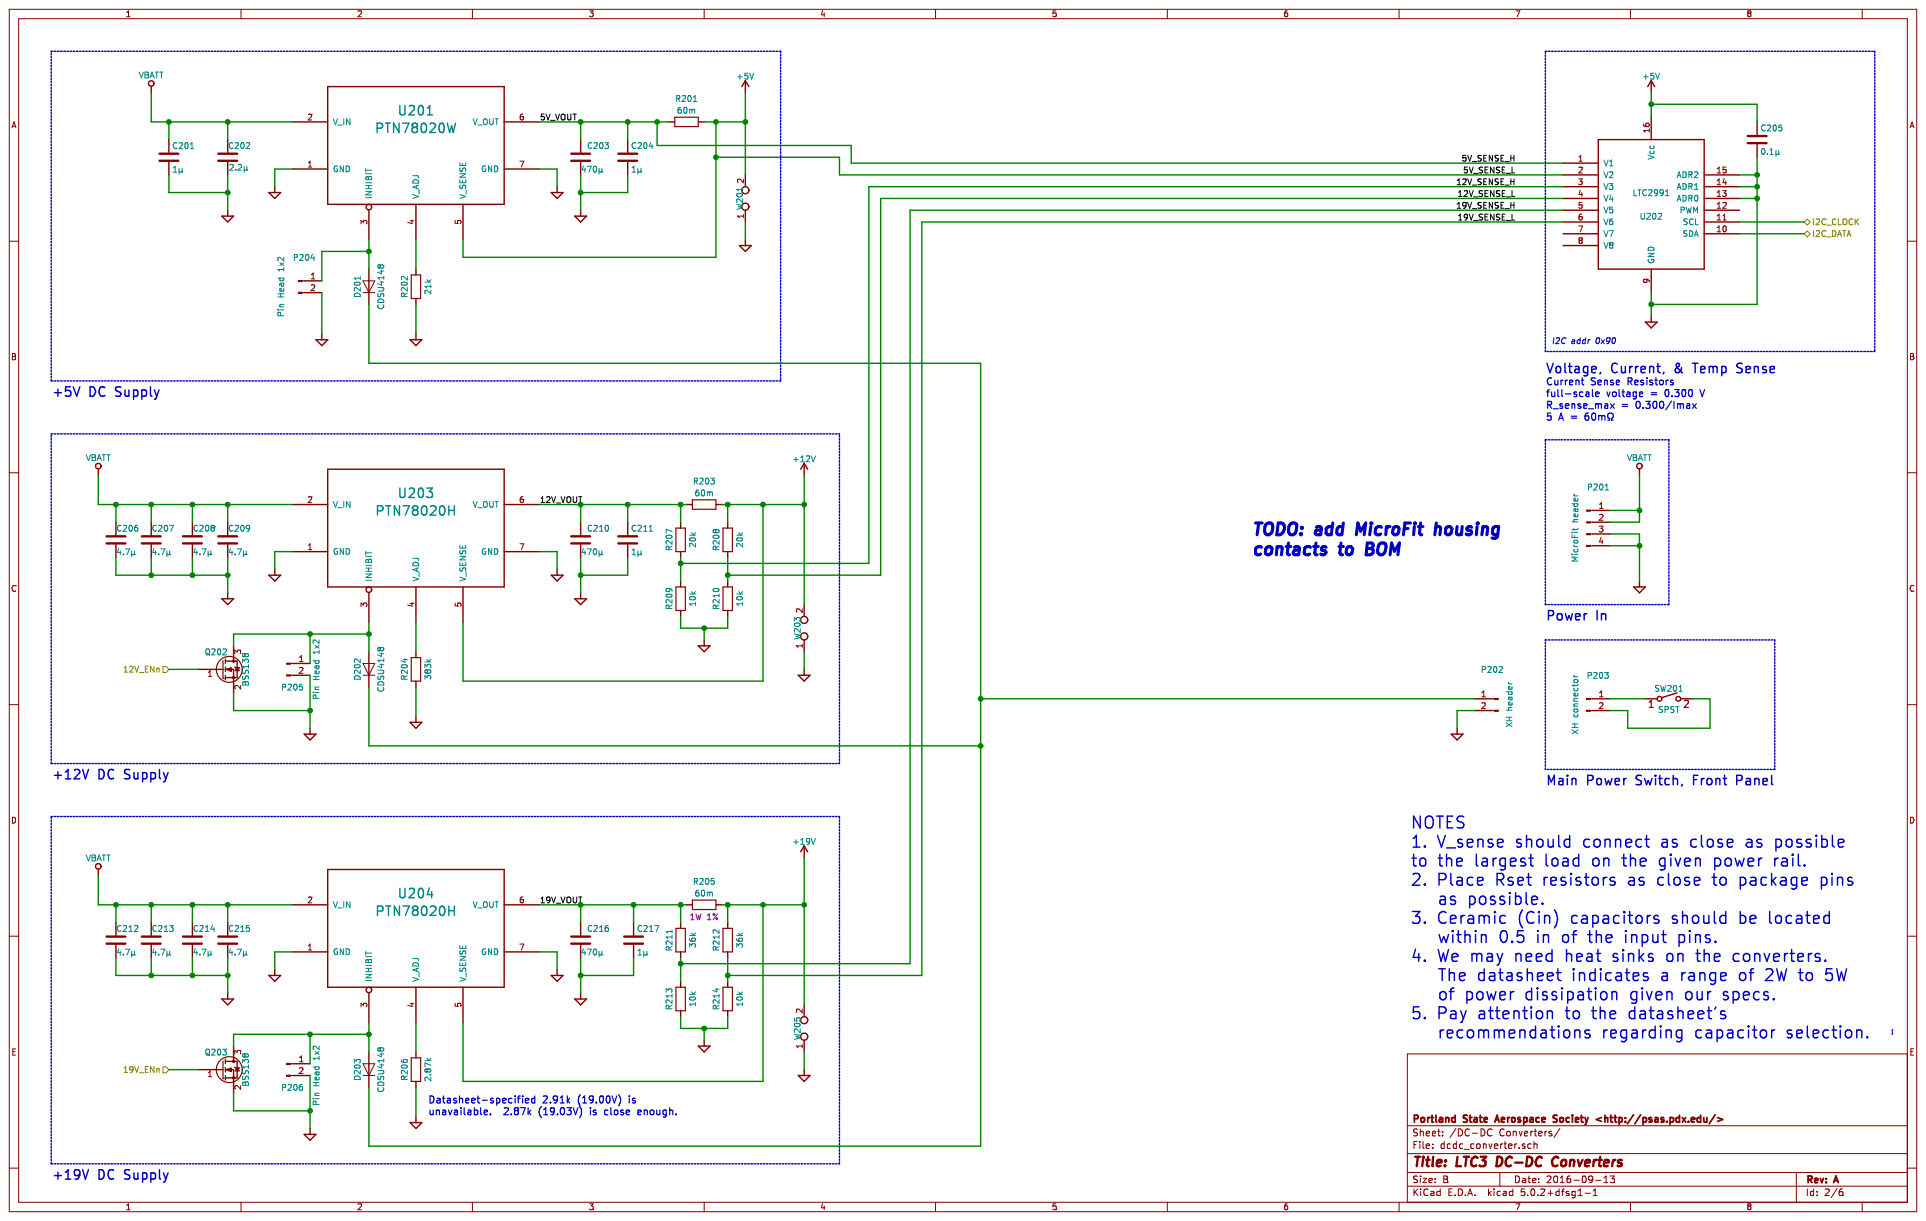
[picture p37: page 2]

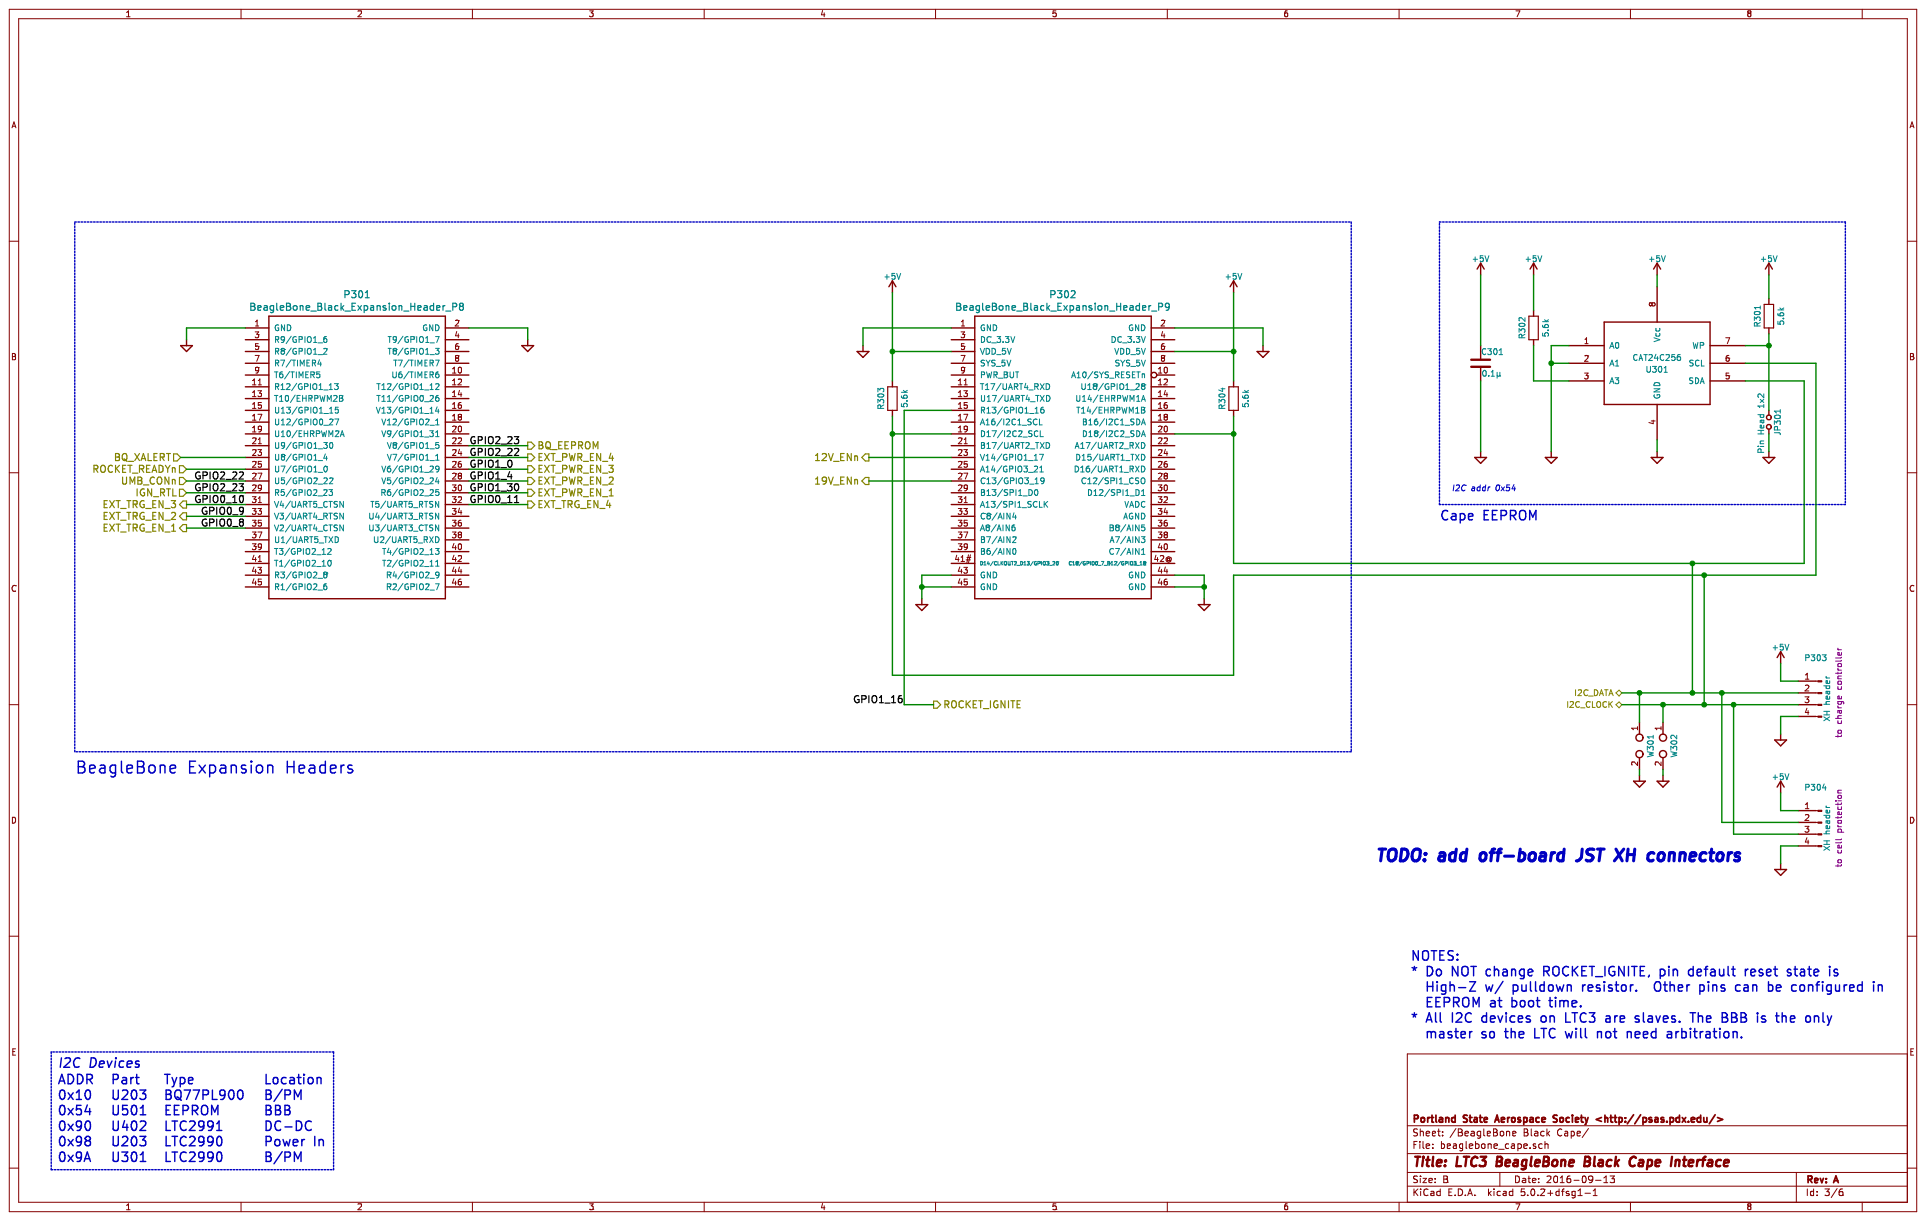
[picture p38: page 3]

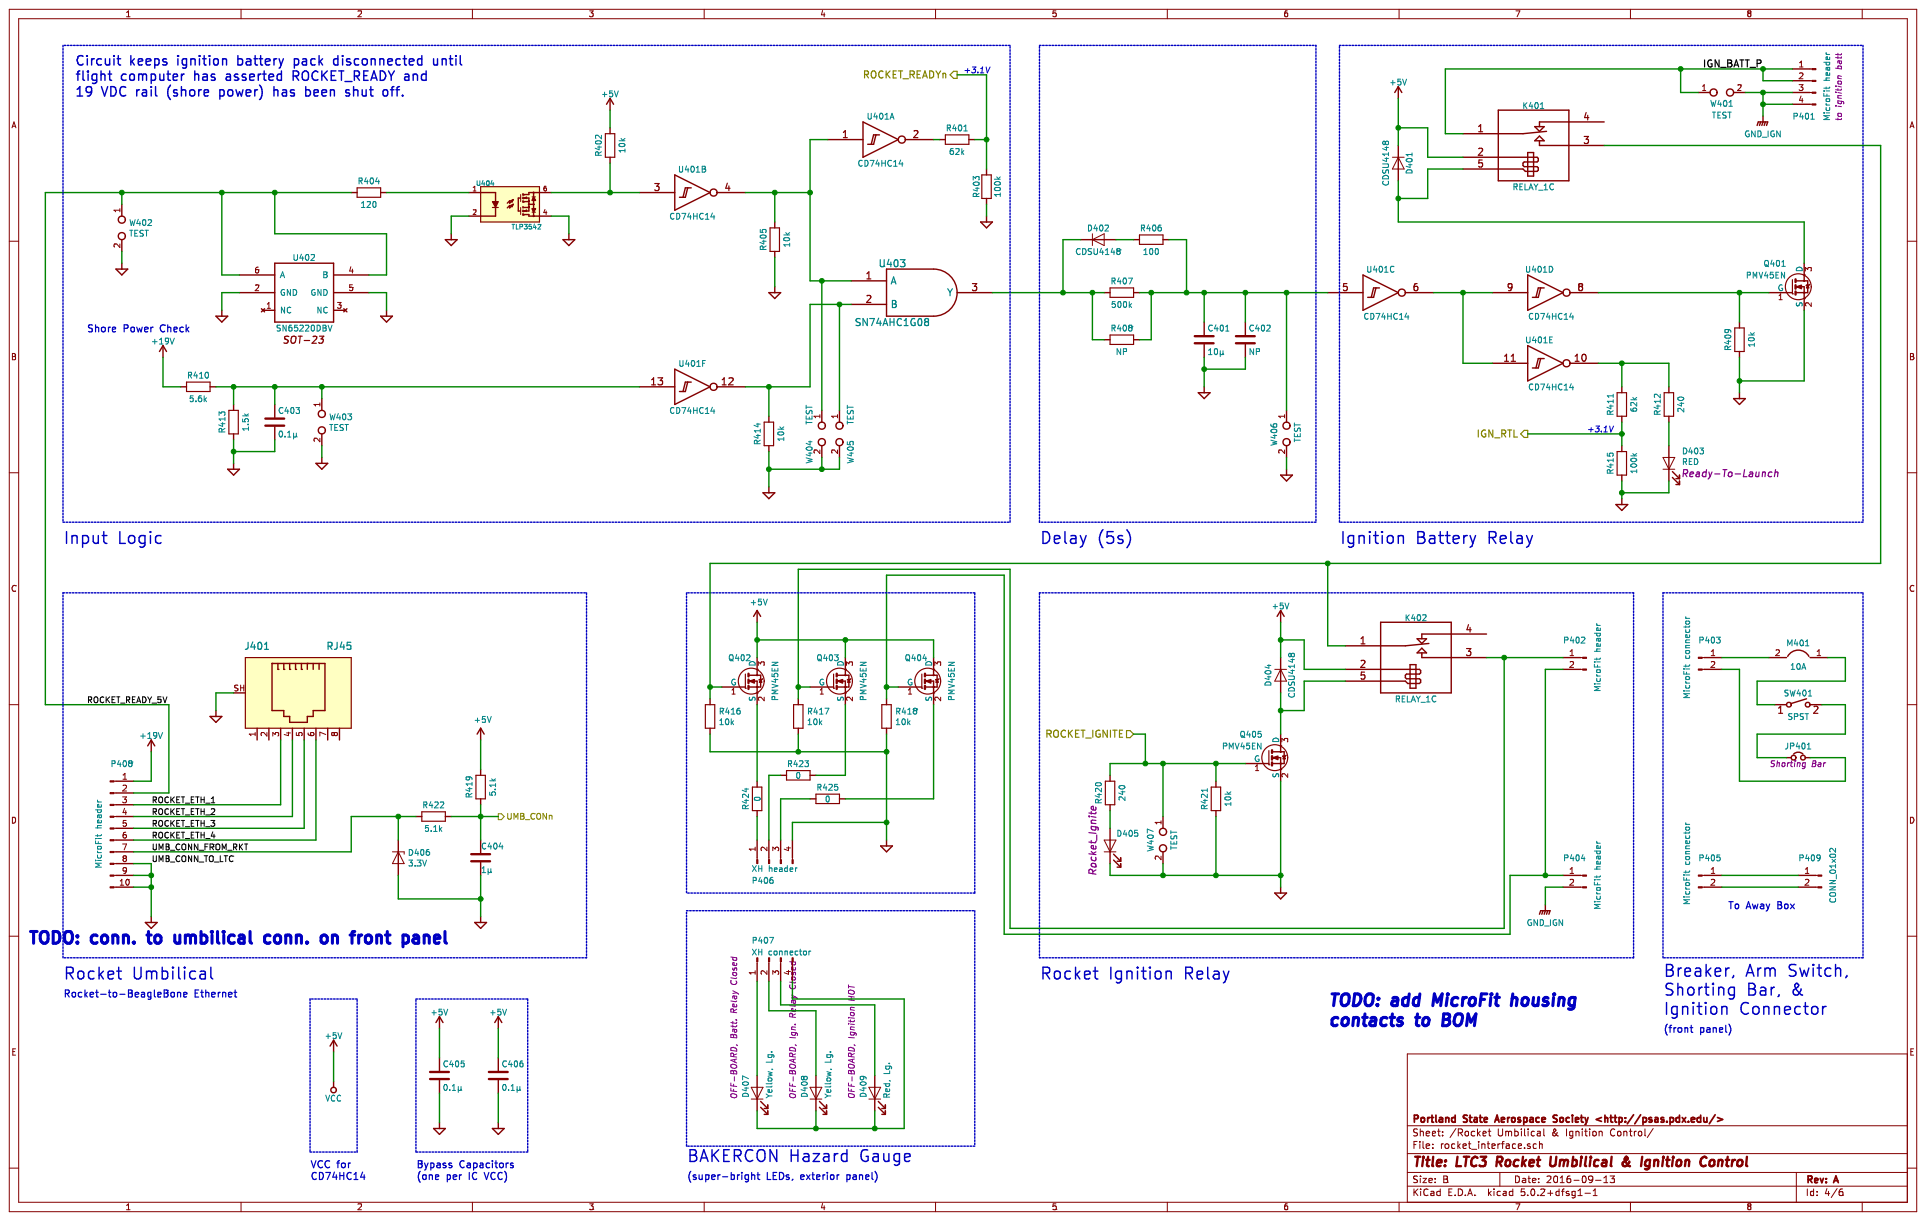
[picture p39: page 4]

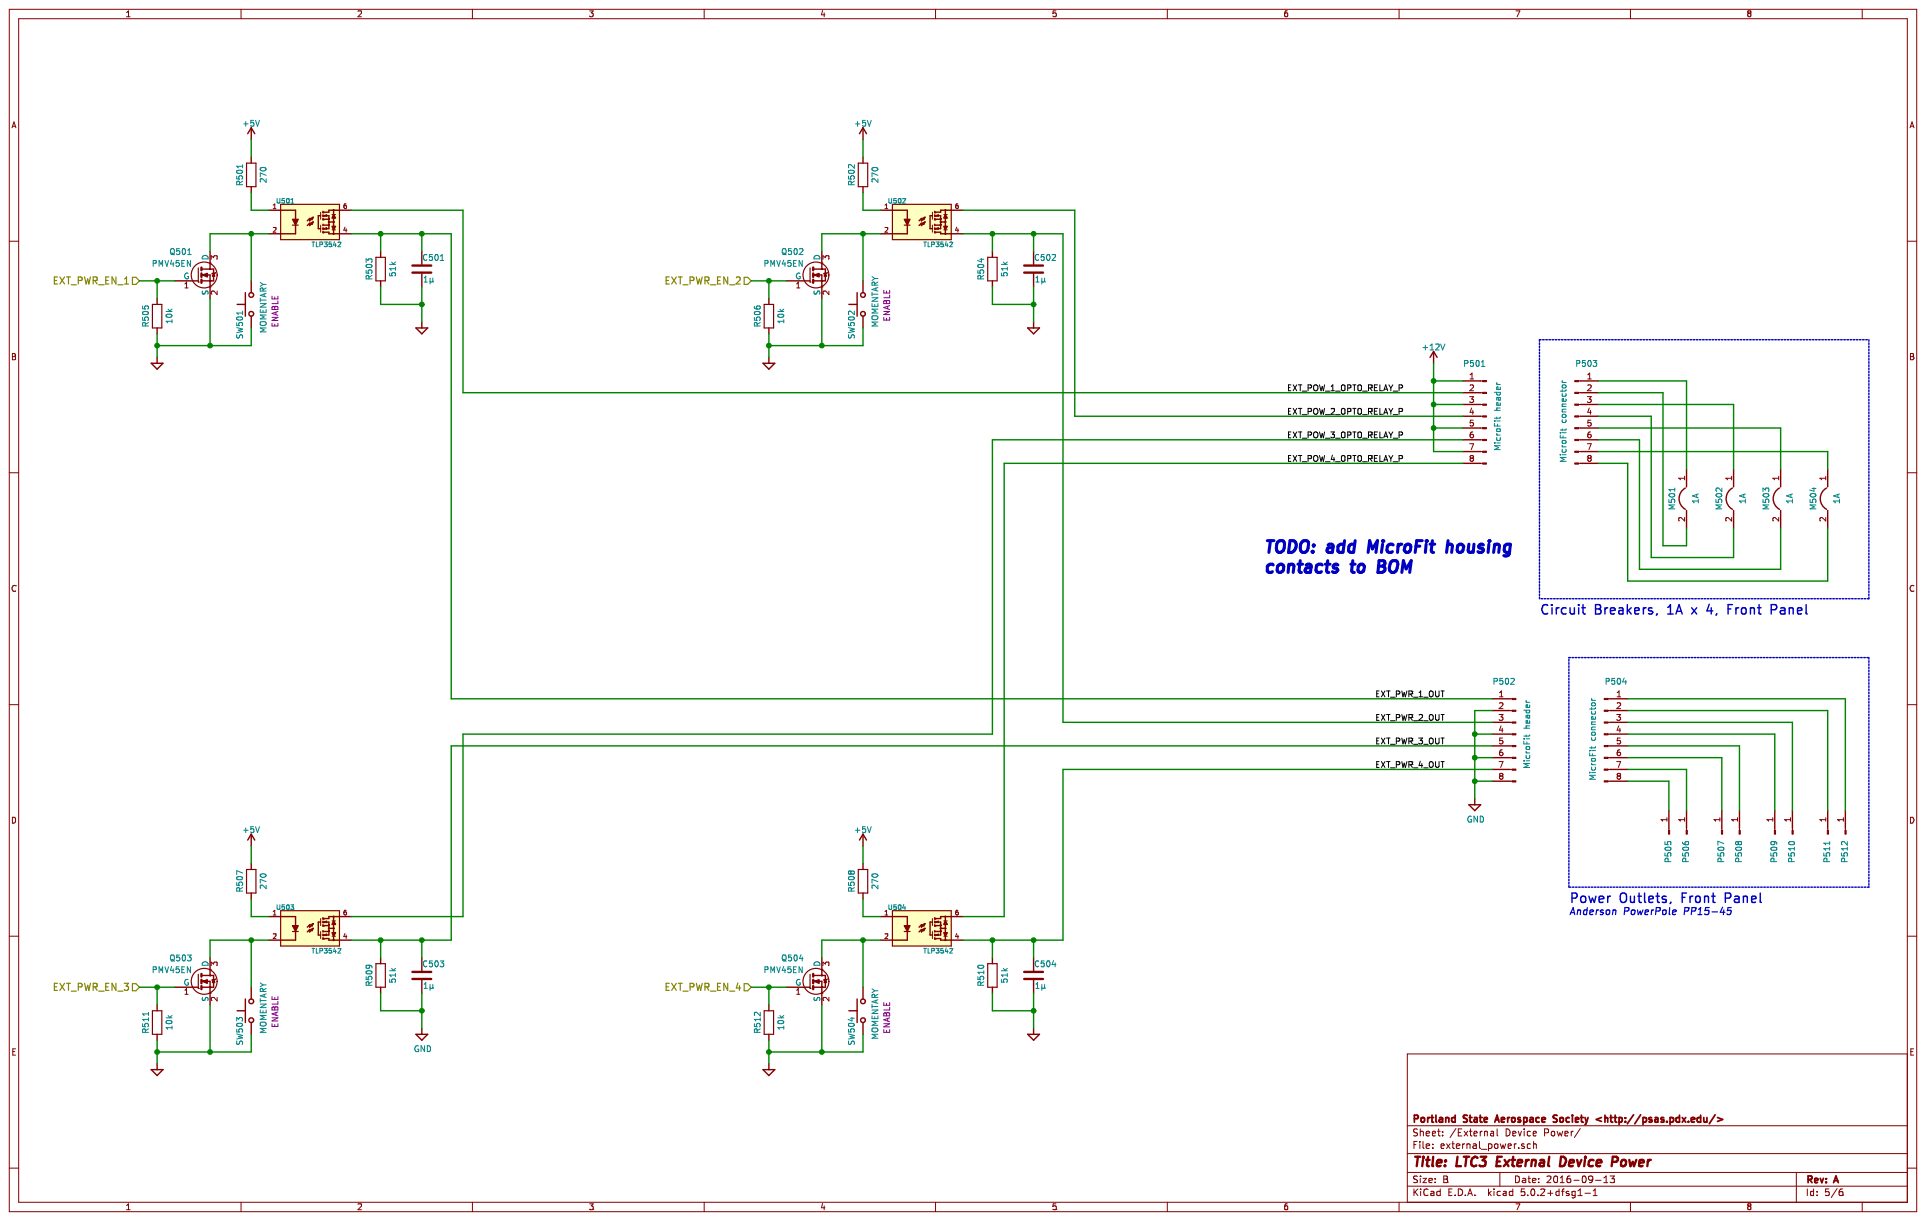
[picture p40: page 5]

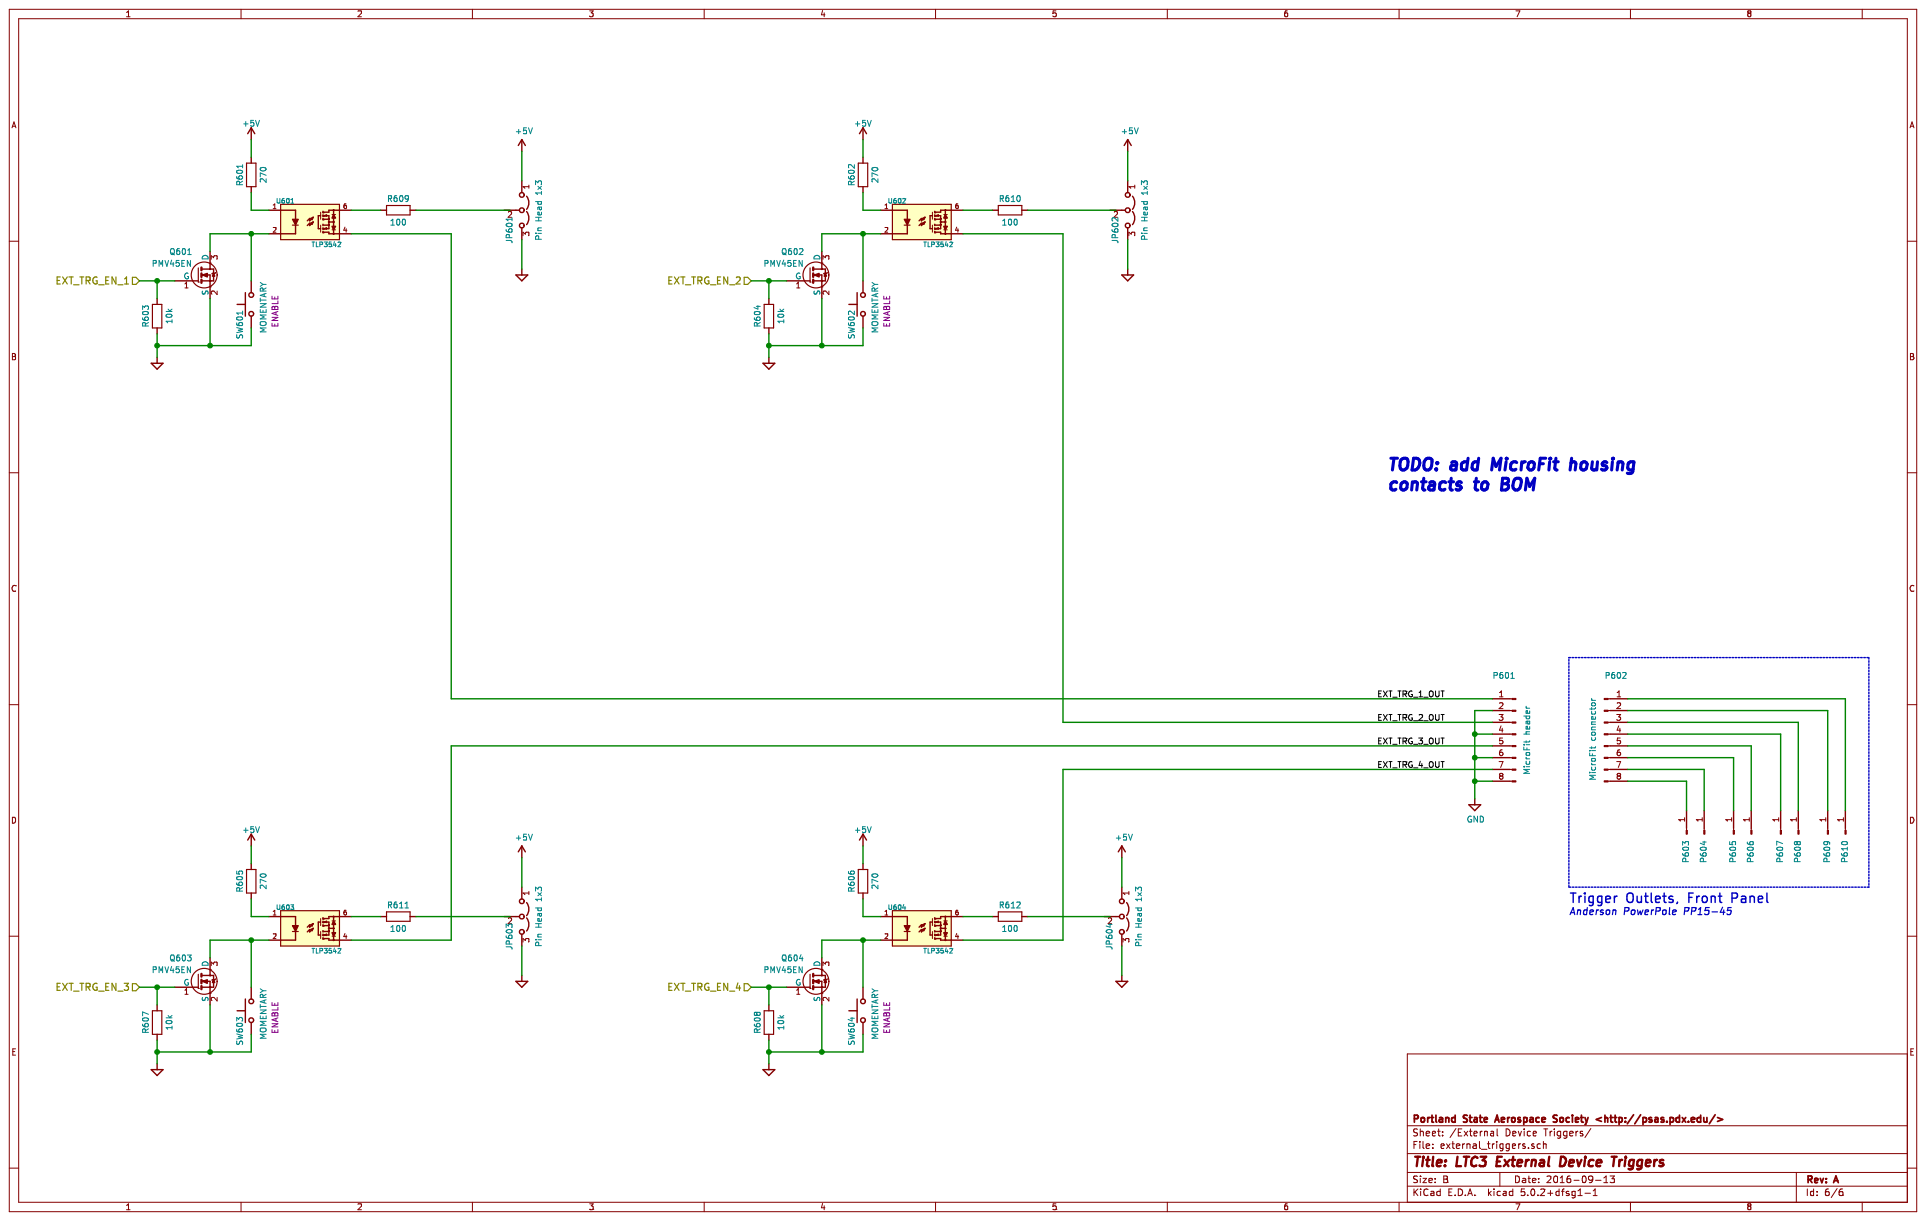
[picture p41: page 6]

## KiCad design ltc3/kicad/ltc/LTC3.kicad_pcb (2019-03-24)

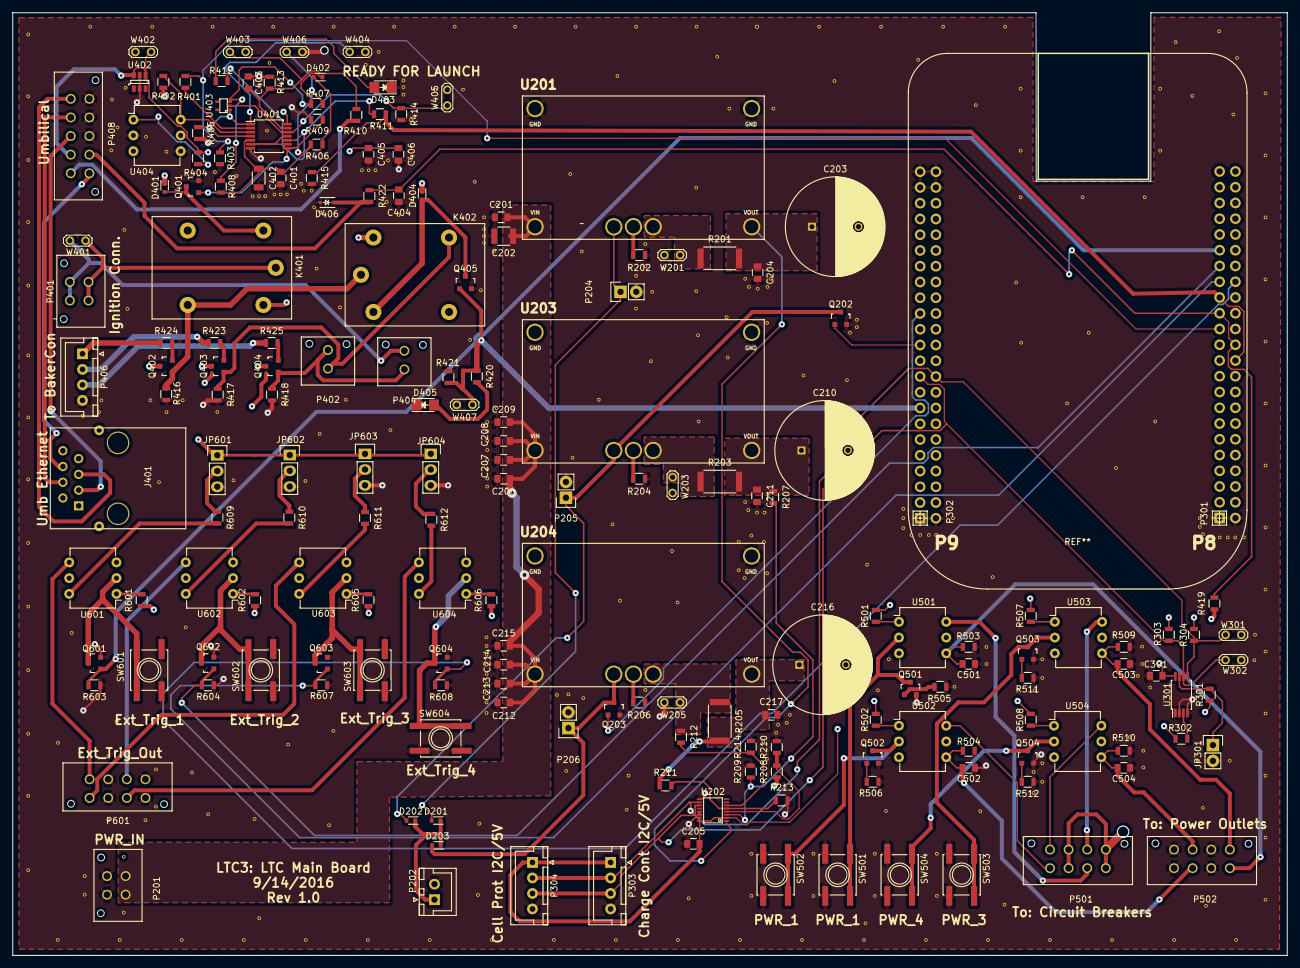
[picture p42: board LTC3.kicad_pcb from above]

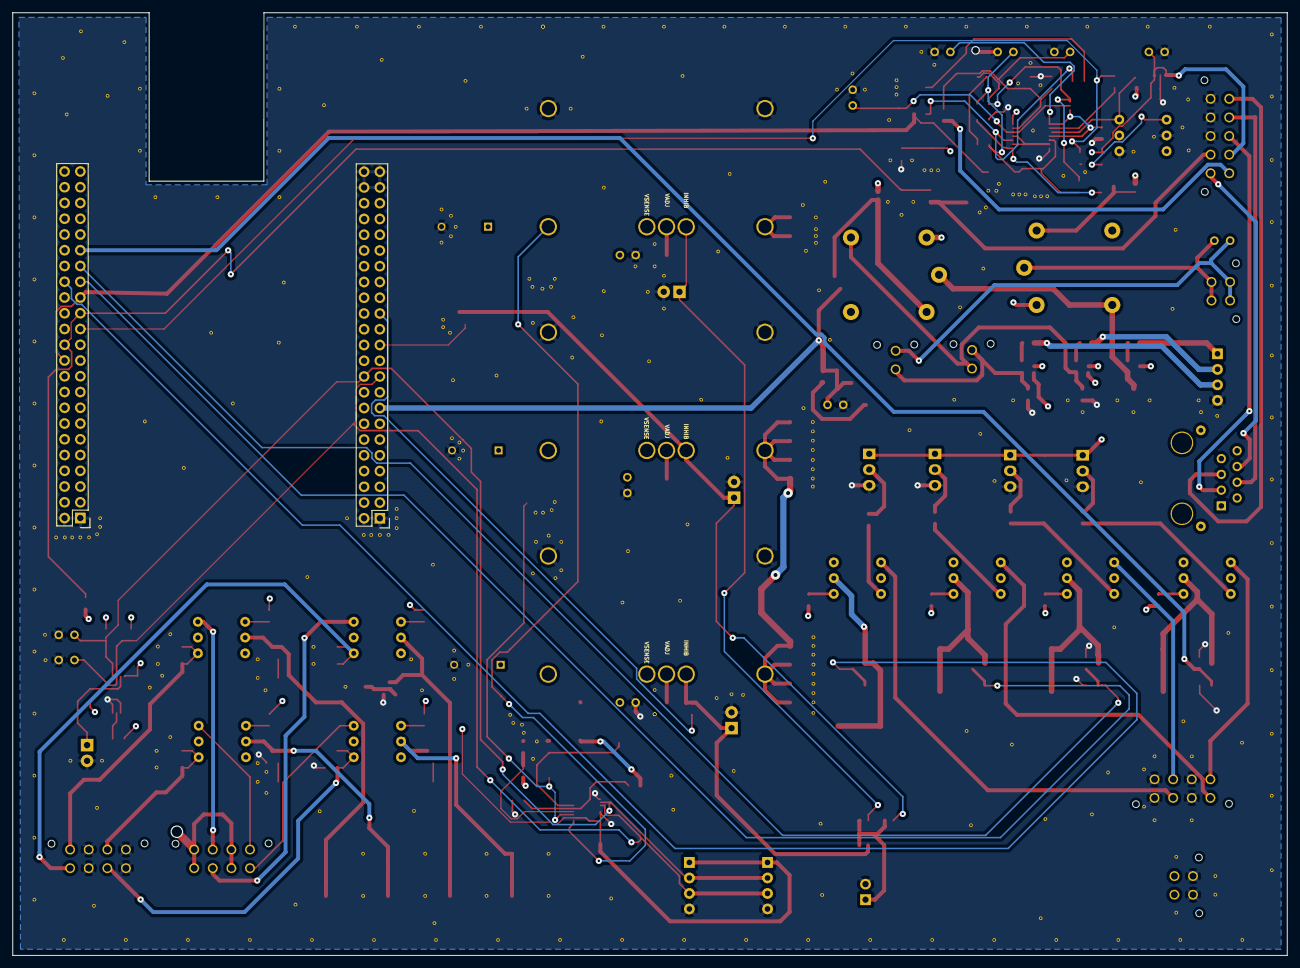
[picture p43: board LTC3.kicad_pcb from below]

Board: 4 copper layers, 205.5 x 152.0 mm, 181 parts (2 on the bottom side), 106 nets.

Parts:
C201, C204, C211, C217, C404, C501, C502, C503, C504: 1μ; C_0805
C202: 2.2μ; C_1210
C203, C210, C216: 470μ; C_Radial_D16_L25_P7.5
C205, C301, C403, C405, C406: 0.1μ; C_0805
C206, C207, C208, C209, C212, C213, C214, C215: 4.7μ; C_0805
C401: 10μ; C_0805
C402: NP; C_1206
D201, D202, D203, D401, D402, D404: CDSU4148; SOD-523
D403, D405: RED; LED_1206
D406: 3.3V; SOD-323
J401: RJ45; RJ45_8_SHIELDED
JP301: Pin Head 1x2; Pin_Header_Straight_1x02
JP601, JP602, JP603, JP604: Pin Head 1x3; Pin_Header_Straight_1x03
K401, K402: RELAY_1C; G5LE-14
P201, P401: MicroFit header; Molex_Microfit3_Header_02x02_Straight_43045-0428
P202: XH header; JST_XH_B02B-XH-A_02x2.50mm_Straight
P204, P205, P206: Pin Head 1x2; Pin_Header_Straight_1x02
P301: BeagleBone_Black_Expansion_Header_P8; Pin_Header_Straight_2x23
P302: BeagleBone_Black_Expansion_Header_P9; Pin_Header_Straight_2x23
P303, P304, P406: XH header; JST_XH_B04B-XH-A_04x2.50mm_Straight
P402, P404: MicroFit header; Molex_Microfit3_Header_02x01_Straight_43045-0228
P408: MicroFit header; Molex_Microfit3_Header_02x05_Straight_43045-1028
P501, P502, P601: MicroFit header; Molex_Microfit3_Header_02x04_Straight_43045-0828
Q202, Q203: BSS138; SOT-23
Q401, Q402, Q403, Q404, Q405, Q501, Q502, Q503, Q504, Q601, Q602, Q603, Q604: PMV45EN; SOT-23
R201, R203, R205: 60m; R_2512
R202: 21k; R_0805
R204: 383k; R_0805
R206: 2.87k; R_0805
R207, R208: 20k; R_0805
R209, R210, R213, R214, R402, R405, R409, R414, R416, R417, R418, R421, R505, R506, R511, R512, R603, R604, R607, R608: 10k; R_0805
R211, R212: 36k; R_0805
R301, R302, R303, R304, R410: 5.6k; R_0805
R401, R411: 62k; R_0805
R403, R415: 100k; R_0805
R404: 120; R_0805
R406, R609, R610, R611, R612: 100; R_0805
R407: 500k; R_0805
R408: NP; R_0805
R412, R420: 240; R_0805
R413: 1.5k; R_0805
R419, R422: 5.1k; R_0805
R423, R424, R425: 0; R_0805
R501, R502, R507, R508, R601, R602, R605, R606: 270; R_0805
R503, R504, R509, R510: 51k; R_0805
SW501, SW502, SW503, SW504, SW601, SW602, SW603, SW604: MOMENTARY; SW_SPST_EVQQ2
U201: PTN78020W
U202: LTC2991; MSOP-16
U203, U204: PTN78020H; PTN78020W
U301: CAT24C256; TSSOP-8_4.4x3mm_Pitch0.65mm
U401: CD74HC14; TSSOP-14_4.4x5mm_Pitch0.65mm
U402: SN65220DBV; SOT-23-6
U403: SN74AHC1G08; SC-70-5
U404, U501, U502, U503, U504, U601, U602, U603, U604: TLP3542; DIP-6_W7.62mm
W201, W203, W205, W301, W302, W401, W402, W403, W404, W405, W406, W407: TEST; Test_Point_2Pads

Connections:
+5V: C205.1, C301.1, C405.1, C406.1, D401.1, D404.1, JP601.1, JP602.1, JP603.1, JP604.1, K401.2, K402.2, P302.5, P302.6, P303.1, P304.1, Q402.3, Q403.3, Q404.3, R201.1, R301.1, R302.1, R303.1, R304.1, R402.1, R419.1, R501.1, R502.1, R507.1, R508.1, R601.1, R602.1, R605.1, R606.1, U201.5, U202.2, U202.16, U301.8, U401.14, W201.2
+12V: P501.1, P501.3, P501.5, P501.7, R203.1, R208.1, U203.5, W203.2
+19V: P408.1, R205.1, R212.1, R410.2, U204.5, W205.2
/BeagleBone Black Cape/12V_ENn: P302.23, Q202.1
/BeagleBone Black Cape/19V_ENn: P302.27, Q203.1
/BeagleBone Black Cape/BQ_EEPROM: P301.22, P301.29, R411.2, R415.1
/BeagleBone Black Cape/EXT_PWR_EN_4: C404.1, P301.24, P301.27, R419.2, R422.1
/BeagleBone Black Cape/EXT_TRG_EN_1: P301.35, Q601.1, R603.1
/BeagleBone Black Cape/EXT_TRG_EN_2: P301.33, Q602.1, R604.1
/BeagleBone Black Cape/EXT_TRG_EN_3: P301.31, Q603.1, R607.1
/BeagleBone Black Cape/EXT_TRG_EN_4: P301.32, Q604.1, R608.1
/BeagleBone Black Cape/I2C_CLOCK: P302.19, P303.3, P304.3, R303.2, U202.11, U301.6, W302.1
/BeagleBone Black Cape/I2C_DATA: P302.20, P303.2, P304.2, R304.2, U202.10, U301.5, W301.1
/BeagleBone Black Cape/ROCKET_IGNITE: P302.15, Q405.1, R420.1, R421.1, W407.1
/BeagleBone Black Cape/ROCKET_READYn: P301.25, R401.1, R403.2
/DC-DC Converters/5V_SENSE_H: C203.1, C204.1, R201.2, U201.6, U202.1
/DC-DC Converters/12V_SENSE_H: R207.2, R209.1, U202.3
/DC-DC Converters/12V_SENSE_L: R208.2, R210.1, U202.4
/DC-DC Converters/12V_VOUT: C210.1, C211.1, R203.2, R207.1, U203.6
/DC-DC Converters/19V_SENSE_H: R211.2, R213.1, U202.5
/DC-DC Converters/19V_SENSE_L: R212.2, R214.1, U202.6
/DC-DC Converters/19V_VOUT: C216.1, C217.1, R205.2, R211.1, U204.6
/External Device Power/EXT_POW_1_OPTO_RELAY_P: P501.2, U501.6
/External Device Power/EXT_POW_2_OPTO_RELAY_P: P501.4, U502.6
/External Device Power/EXT_POW_3_OPTO_RELAY_P: P501.6, U503.6
/External Device Power/EXT_POW_4_OPTO_RELAY_P: P501.8, U504.6
/External Device Power/EXT_PWR_1_OUT: C501.1, P502.1, R503.1, U501.4
/External Device Power/EXT_PWR_2_OUT: C502.1, P502.3, R504.1, U502.4
/External Device Power/EXT_PWR_3_OUT: C503.1, P502.5, R509.1, U503.4
/External Device Power/EXT_PWR_4_OUT: C504.1, P502.7, R510.1, U504.4
/External Device Power/EXT_PWR_EN_1: Q501.1, R505.1
/External Device Power/EXT_PWR_EN_2: Q502.1, R506.1
/External Device Power/EXT_PWR_EN_3: Q503.1, R511.1
/External Device Power/EXT_PWR_EN_4: Q504.1, R512.1
/External Device Triggers/EXT_TRG_1_OUT: P601.1, U601.4
/External Device Triggers/EXT_TRG_2_OUT: P601.3, U602.4
/External Device Triggers/EXT_TRG_3_OUT: P601.5, U603.4
/External Device Triggers/EXT_TRG_4_OUT: P601.7, U604.4
/Rocket Umbilical & Ignition Control/IGN_BATT_P: K401.1, P401.1, P401.2, W401.2
/Rocket Umbilical & Ignition Control/ROCKET_ETH_1: J401.3, P408.3
/Rocket Umbilical & Ignition Control/ROCKET_ETH_2: J401.4, P408.4
/Rocket Umbilical & Ignition Control/ROCKET_ETH_3: J401.5, P408.5
/Rocket Umbilical & Ignition Control/ROCKET_ETH_4: J401.6, P408.6
/Rocket Umbilical & Ignition Control/ROCKET_READY_5V: P408.2, R404.2, U402.4, U402.6, W402.1
/Rocket Umbilical & Ignition Control/UMB_CONN_FROM_RKT: D406.1, P408.7, R422.2
GND: C201.2, C202.2, C203.2, C204.2, C205.2, C206.2, C207.2, C208.2, C209.2, C210.2, C211.2, C212.2, C213.2, C214.2, C215.2, C216.2, C217.2, C301.2, C401.2, C402.2, C403.2, C404.2, C405.2, C406.2, C501.2, C502.2, C503.2, C504.2, D403.1, D405.1, D406.2, JP301.2, JP601.3, JP602.3, JP603.3, JP604.3, P201.3, P201.4, P202.2, P204.2, P205.2, P206.2, P301.1, P301.2, P302.1, P302.2, P302.43, P302.44, P302.45, P302.46, P303.4, P304.4, P406.4, P408.8, P408.9, P408.10, P502.2, P502.4, P502.6, P502.8, P601.2, P601.4, P601.6, P601.8, Q202.2, Q203.2, Q401.2, Q405.2, Q501.2, Q502.2, Q503.2, Q504.2, Q601.2, Q602.2, Q603.2, Q604.2, R202.2, R204.2, R206.2, R209.2, R210.2, R213.2, R214.2, R403.1, R405.2, R409.2, R413.2, R414.2, R415.2, R416.2, R417.2, R418.2, R421.2, R503.2, R504.2, R505.2, R506.2, R509.2, R510.2, R511.2, R512.2, R603.2, R604.2, R607.2, R608.2, SW501.2, SW502.2, SW503.2, SW504.2, SW601.2, SW602.2, SW603.2, SW604.2, U201.1, U201.7, U202.9, U202.13, U202.14, U202.15, U203.1, U203.7, U204.1, U204.7, U301.1, U301.2, U301.4, U401.7, U402.2, U402.5, U404.2, U404.4, W201.1, W203.1, W205.1, W301.2, W302.2, W402.2, W403.2, W404.2, W405.2, W406.2, W407.2
GND_IGN: P401.3, P401.4, P404.2, W401.1
unnamed: C401.1, C402.1, R406.1, R407.1, R408.1, U401.5, W406.1
unnamed: C403.1, R410.1, R413.1, U401.13, W403.1
unnamed: D201.1, D202.1, D203.1, P202.1
unnamed: D201.2, P204.1, U201.3
unnamed: D202.2, P205.1, Q202.3, U203.3
unnamed: D203.2, P206.1, Q203.3, U204.3
unnamed: D401.2, K401.5, Q401.3
unnamed: D402.1, R407.2, R408.2, U403.3
unnamed: D402.2, R406.2
unnamed: D403.2, R412.2
unnamed: D404.2, K402.5, Q405.3
unnamed: D405.2, R420.2
unnamed: JP301.1, R301.2, U301.7
unnamed: JP601.2, R609.1
unnamed: JP602.2, R610.1
unnamed: JP603.2, R611.1
unnamed: JP604.2, R612.1
unnamed: K401.3, K402.1, Q402.1, R416.1
unnamed: K402.3, P402.1, Q403.1, R417.1
unnamed: P402.2, P404.1, Q404.1, R418.1
unnamed: P406.1, R424.2
unnamed: P406.2, R423.2
unnamed: P406.3, R425.2
unnamed: Q401.1, R409.1, U401.8
unnamed: Q402.2, R424.1
unnamed: Q403.2, R423.1
unnamed: Q404.2, R425.1
unnamed: Q501.3, SW501.1, U501.2
unnamed: Q502.3, SW502.1, U502.2
unnamed: Q503.3, SW503.1, U503.2
unnamed: Q504.3, SW504.1, U504.2
unnamed: Q601.3, SW601.1, U601.2
unnamed: Q602.3, SW602.1, U602.2
unnamed: Q603.3, SW603.1, U603.2
unnamed: Q604.3, SW604.1, U604.2
unnamed: R202.1, U201.4
unnamed: R204.1, U203.4
unnamed: R206.1, U204.4
unnamed: R302.2, U301.3
unnamed: R401.2, U401.2
unnamed: R402.2, U401.3, U404.6
unnamed: R404.1, U404.1
unnamed: R405.1, U401.1, U401.4, U403.1, W404.1
unnamed: R411.1, R412.1, U401.10
unnamed: R414.1, U401.12, U403.2, W405.1
unnamed: R501.2, U501.1
unnamed: R502.2, U502.1
unnamed: R507.2, U503.1
unnamed: R508.2, U504.1
unnamed: R601.2, U601.1
unnamed: R602.2, U602.1
unnamed: R605.2, U603.1
unnamed: R606.2, U604.1
unnamed: R609.2, U601.6
unnamed: R610.2, U602.6
unnamed: R611.2, U603.6
unnamed: R612.2, U604.6
unnamed: U401.6, U401.9, U401.11
VBATT: C201.1, C202.1, C206.1, C207.1, C208.1, C209.1, C212.1, C213.1, C214.1, C215.1, P201.1, P201.2, U201.2, U203.2, U204.2

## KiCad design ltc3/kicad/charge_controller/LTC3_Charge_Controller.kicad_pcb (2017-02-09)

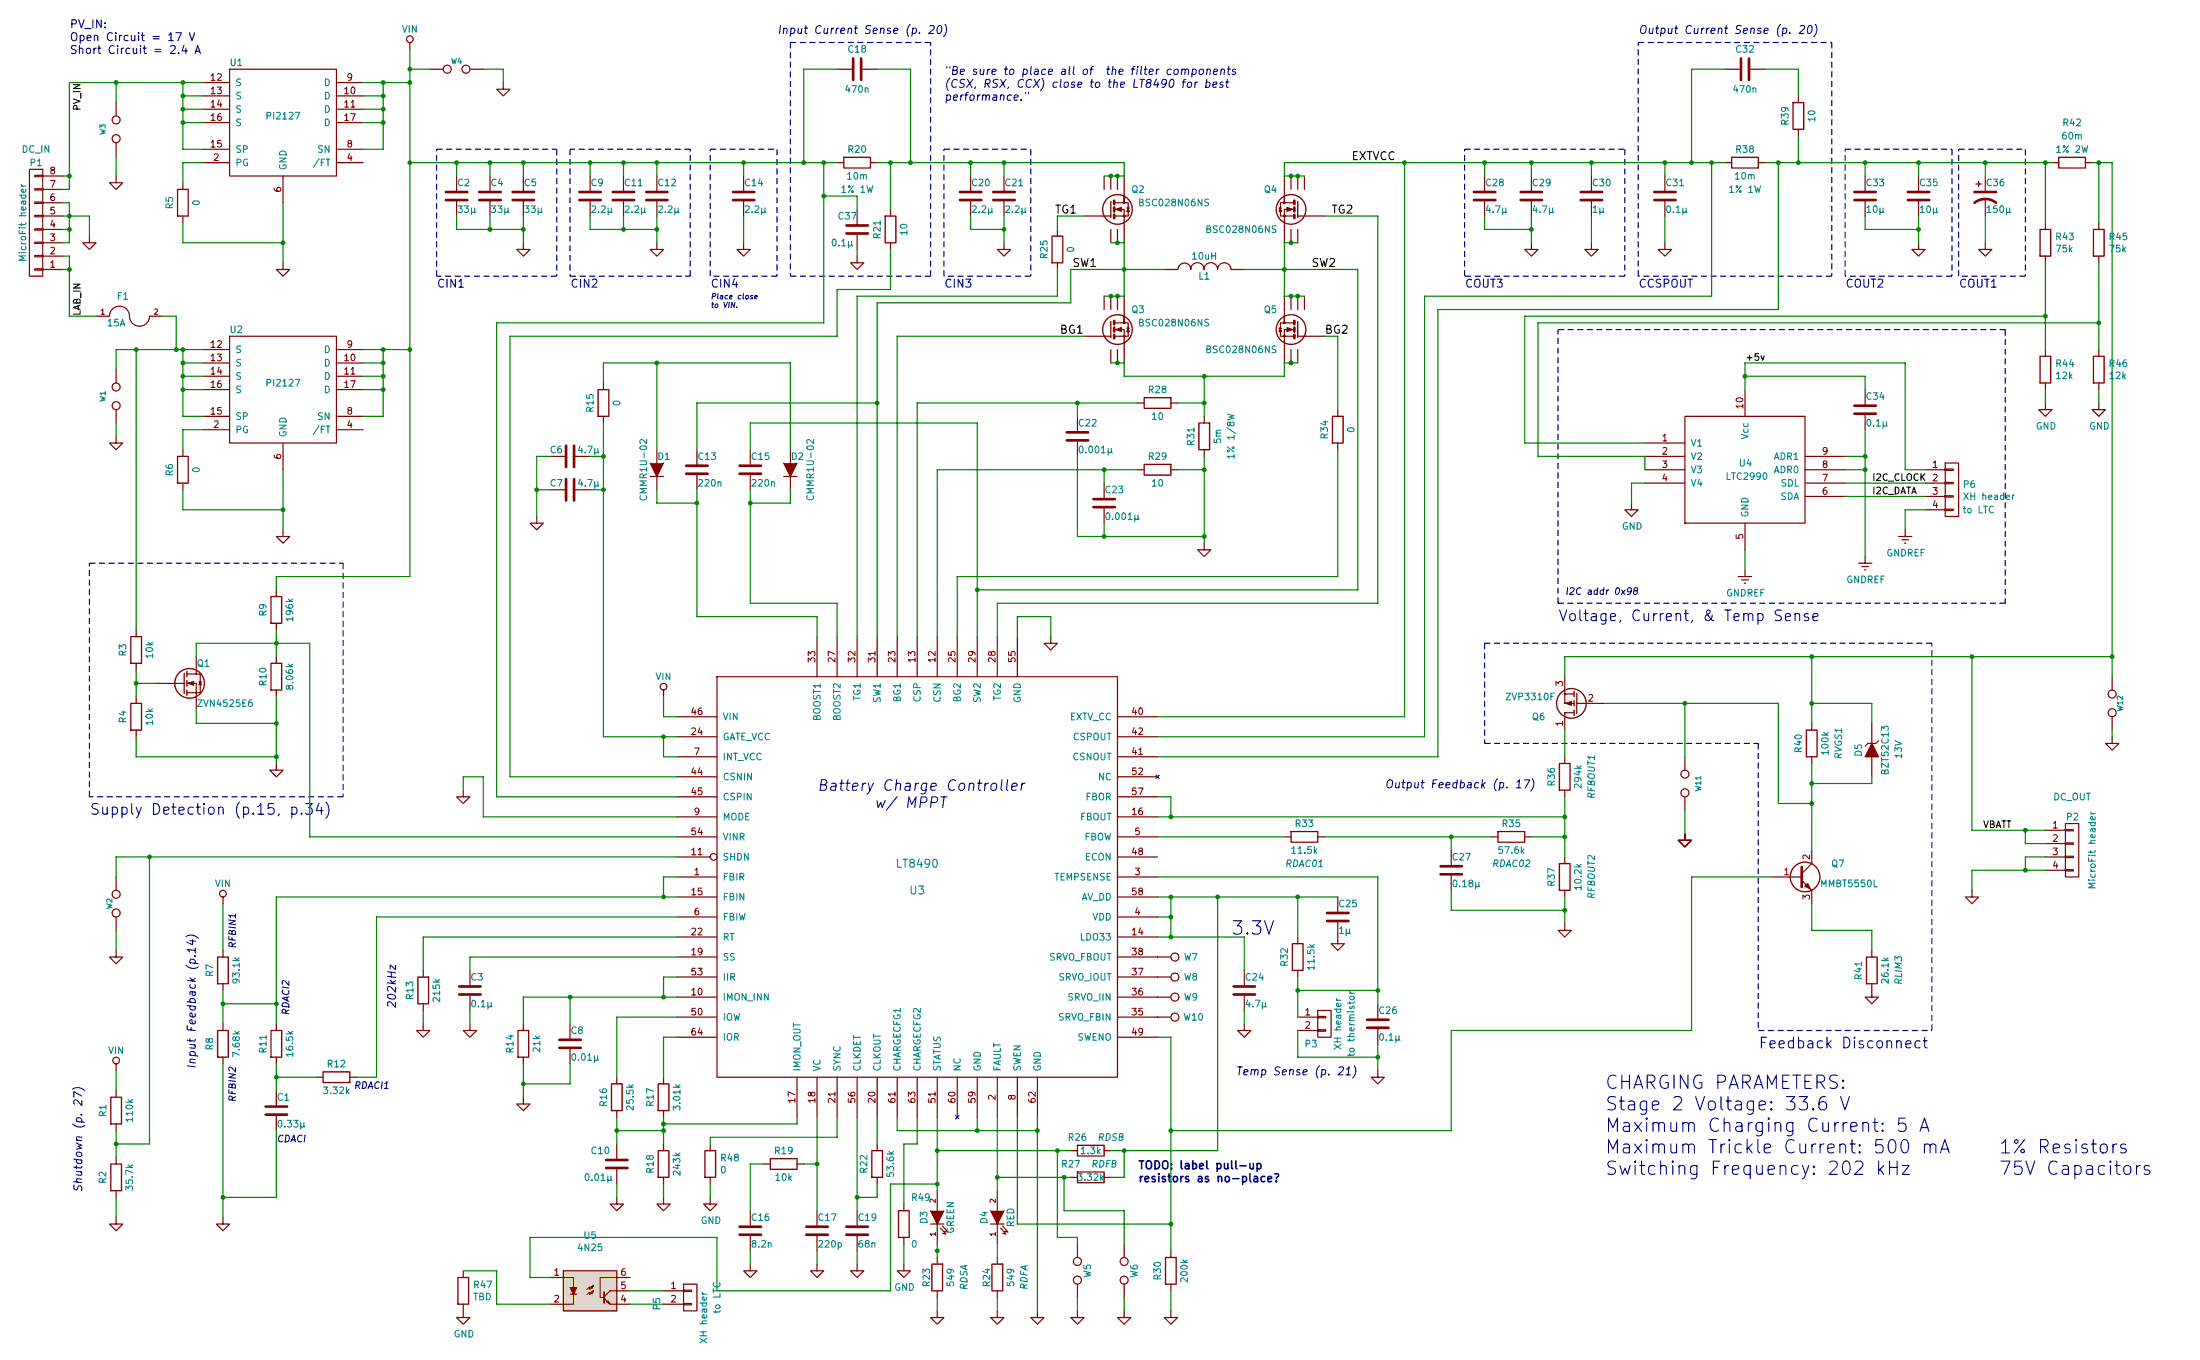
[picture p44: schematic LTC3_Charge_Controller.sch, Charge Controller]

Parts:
C1: 0.33μ; C_0805; Mfg_PN GRM21AR72A334KAC5L
C2, C4, C5: 33μ; c_elec_10x10; Mfg_PN UUX2A330MNL1GS
C3, C26, C31: 0.1μ; C_0805; Mfg_PN GCM21BR72A104KA37L
C6, C7, C24: 4.7μ; C_0805; Mfg_PN GRM21BR71C475KA73L
C8, C10: 0.01μ; C_0805; Mfg_PN GRM216R71H103JA01D
C9, C11, C12, C14, C20, C21: 2.2μ; C_1210; Mfg_PN GRM32ER72A225KA35L
C13, C15: 220n; C_0805; Mfg_PN GRM21BR71H224KA01L
C16: 8.2n; C_0805; Mfg_PN GRM21BR71H823KA01L
C17: 220p; C_0805; Mfg_PN CC0805KRX7R9BB221
C18, C32: 470n; C_0805; Mfg_PN GRM21BR71H474KA88L
C19: 68n; C_0805; Mfg_PN GRM219R71E683KA01D
C22, C23: 0.001μ; C_0805; Mfg_PN GRM216R71H102JA01D
C25: 1μ; C_0805; Mfg_PN GRM21BR71E105KA99K
C27: 0.18μ; C_0805; Mfg_PN GRM21BR71H184KA01L
C28, C29: 4.7μ; C_2220; Mfg_PN GRM55ER72A475KA01L
C30: 1μ; C_0805; Mfg_PN GRJ21BC72A105KE11L
C33, C35: 10μ; c_elec_6.3x7.7; Mfg_PN UCD1K100MCL1GS
C34: 0.1μ; C_0805; Mfg_PN GRM21BR71E104KA01L
C36: 150μ; C_Radial_D12.5_L25_P5; Mfg_PN UPW2A151MHD
C37: 0.1μ; C_0805; Mfg_PN GRM21BR71H104KA01L
D1, D2: CMMR1U-02; SOD-123; Mfg_PN CMMR1U-02 TR
D3: GREEN; LED_1206; Mfg_PN LTST-C150GKT
D4: RED; LED_1206; Mfg_PN LTST-C150CKT
D5: BZT52C13; SOD-123; Mfg_PN BZT52C13-7-F
F1: 15A; Fuseholder_Auto_Blade_Regular_Keystone_3557-2; Mfg_PN 3557-2
L1: 10uH; Coilcraft_SER2900; Mfg_PN SER2915L-103KL
P1: MicroFit header; Molex_Microfit3_Header_02x04_Straight_43045-0828; Mfg_PN 43045-0828
P2: MicroFit header; Molex_Microfit3_Header_02x02_Straight_43045-0428; Mfg_PN 43045-0428
P3: XH header; JST_XH_B02B-XH-A_02x2.50mm_Straight; Mfg_PN B2B-XH-A(LF)(SN)
P5: XH header; JST_EH_B02B-XH-A_02x2.50mm_Straight; Mfg_PN B2B-XH-A(LF)(SN)
P6: XH header; JST_EH_B04B-XH-A_04x2.50mm_Straight; Mfg_PN B4B-XH-A(LF)(SN)
Q1: ZVN4525E6; SOT-26; Mfg_PN ZVN4525E6TA
Q2, Q3, Q4, Q5: BSC028N06NS; SO-8; Mfg_PN BSC028N06NS
Q6: ZVP3310F; SOT-23; Mfg_PN ZVP3310FTA
Q7: MMBT5550L; SOT-23; Mfg_PN MMBT5550LT1G
R1: 110k; R_0805; Mfg_PN RC0805FR-07110KL
R2: 35.7k; R_0805; Mfg_PN RC0805FR-0735K7L
R3, R4, R19: 10k; R_0805; Mfg_PN RC0805FR-0710KL
R5, R6, R48, R49: 0; R_0805; Mfg_PN RC0805JR-070RL
R7: 93.1k; R_0805; Mfg_PN RC0805FR-0793K1L
R8: 7.68k; R_0805; Mfg_PN RC0805FR-077K68L
R9: 196k; R_0805; Mfg_PN RC0805FR-07196KL
R10: 8.06k; R_0805; Mfg_PN MCR10EZHF8061
R11: 16.5k; R_0805; Mfg_PN RC0805FR-0716K5L
R12, R27: 3.32k; R_0805; Mfg_PN RC0805FR-073K32L
R13: 215k; R_0805; Mfg_PN RC0805FR-07215KL
R14: 21k; R_0805; Mfg_PN RC0805FR-0721KL
R15, R25, R34: 0; R_0603; Mfg_PN RC0603JR-070RL
R16: 25.5k; R_0805; Mfg_PN CRCW080527K1FKTA
R17: 3.01k; R_0805; Mfg_PN RC0805FR-073K01L
R18: 243k; R_0805; Mfg_PN RC0805FR-07243KL
R20, R38: 10m; R_1206; Mfg_PN WSLP1206R0100FEA
R21, R28, R29, R39: 10; R_0805; Mfg_PN RC0805FR-0710RL
R22: 53.6k; R_0805; Mfg_PN RC0805FR-0753K6L
R23, R24: 549; R_0805; Mfg_PN RC0805FR-07549RL
R26: 1.3k; R_0805; Mfg_PN RC0805FR-071K3L
R30: 200k; R_0805; Mfg_PN RC0805FR-07200KL
R31: 5m; R_1206; Mfg_PN WSL12065L000FEA
R32, R33: 11.5k; R_0805; Mfg_PN RC0805FR-0711K5L
R35: 57.6k; R_0805; Mfg_PN RC0805FR-0757K6L
R36: 294k; R_0805; Mfg_PN RC0805FR-07294KL
R37: 10.2k; R_0805; Mfg_PN RC0805FR-0710K2L
R40: 100k; R_0805; Mfg_PN RC0805FR-07100KL
R41: 26.1k; R_0805; Mfg_PN RC0805FR-0726K1L
R42: 60m; R_2512; Mfg_PN PE2512FKE7W0R06L
R43, R45: 75k; R_0805; Mfg_PN RC0805FR-0775KL
R44, R46: 12k; R_0805; Mfg_PN RC0805FR-0712KL
R47: TBD; R_0805
U1, U2: PI2127; LGA-17; Mfg_PN PI2127-01-LGIZ
U3: LT8490; Mfg_PN LT8490IUKJ#PBF
U4: LTC2990; MSOP-10; Mfg_PN LTC2990IMS#PBF
U5: 4N25; DIP-6_W7.62mm; Mfg_PN 4N25
W1, W2, W3, W4, W5, W6, W11, W12: TEST; Test_Point_2Pads
W7, W8, W9, W10: TEST_1P; Measurement_Point_Square-SMD-Pad_Small

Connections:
/+5v: C34.1, P6.1, U4.10 (Vcc)
/BG1: Q3.4 (G), U3.23 (BG1)
/BG2: Q5.4 (G), R34.1
/EXTVCC: C28.1, C29.1, C30.1, C31.1, C32.2, Q4.5 (D), Q4.6 (D), Q4.7 (D), Q4.8 (D), R38.2, U3.40 (EXTV_CC), U3.42 (CSPOUT)
/I2C_CLOCK: P6.2, U4.7 (SDL)
/I2C_DATA: P6.3, U4.6 (SDA)
/LAB_IN: F1.1, P1.1, P1.2
/PV_IN: P1.7, P1.8, U1.12 (S), U1.13 (S), U1.14 (S), U1.15 (SP), U1.16 (S), W3.1
/SW1: C13.1, L1.1, Q2.1 (S), Q2.2 (S), Q2.3 (S), Q3.5 (D), Q3.6 (D), Q3.7 (D), Q3.8 (D), U3.31 (SW1)
/SW2: C15.1, L1.2, Q4.1 (S), Q4.2 (S), Q4.3 (S), Q5.5 (D), Q5.6 (D), Q5.7 (D), Q5.8 (D), U3.29 (SW2)
/TG1: Q2.4 (G), R25.1
/TG2: Q4.4 (G), U3.28 (TG2)
/VBATT: D5.1 (K), P2.1, P2.2, Q6.3 (S), R40.1, R42.1, R45.1, W12.1
GND: C1.2, C2.2, C3.2, C4.2, C5.2, C6.2, C7.2, C8.2, C9.2, C10.2, C11.2, C12.2, C14.2, C16.2, C17.2, C19.2, C20.2, C21.2, C22.2, C23.2, C24.2, C25.2, C26.2, C27.2, C28.2, C29.2, C30.2, C31.2, C33.2, C35.2, C36.2, C37.2, P1.3, P1.4, P1.5, P1.6, P2.3, P2.4, P3.2, Q1.4 (S), R2.2, R4.2, R5.2, R6.2, R8.2, R10.2, R13.1, R14.2, R18.2, R23.1, R24.1, R29.2, R30.2, R31.1, R37.2, R41.2, R44.2, R46.2, R47.2, R48.2, R49.2, U1.6 (GND), U2.6 (GND), U3.9 (MODE), U3.55 (GND), U3.59 (GND), U3.61 (CHARGECFG1), U3.62 (GND), U4.4 (V4), W1.1, W2.2, W3.2, W4.2, W5.2, W6.2, W11.2, W12.2
GNDREF: C34.2, P6.4, U4.5 (GND), U4.8 (ADR0), U4.9 (ADR1)
unnamed: C1.1, R11.2, R12.1
unnamed: C3.1, U3.19 (SS)
unnamed: C6.1, C7.1, R15.2, U3.7 (INT_VCC), U3.24 (GATE_VCC)
unnamed: C8.1, R14.1, U3.10 (IMON_INN), U3.53 (IIR)
unnamed: C10.1, R16.2, R17.2, R18.1, U3.17 (IMON_OUT)
unnamed: C13.2, D1.1 (K), U3.33 (BOOST1)
unnamed: C15.2, D2.1 (K), U3.27 (BOOST2)
unnamed: C16.1, R19.2
unnamed: C17.1, R19.1, U3.18 (VC)
unnamed: C18.1, C20.1, C21.1, Q2.5 (D), Q2.6 (D), Q2.7 (D), Q2.8 (D), R20.1, R21.2
unnamed: C19.1, R22.2, U3.56 (CLKDET)
unnamed: C22.1, R28.1, U3.13 (CSP)
unnamed: C23.1, R29.1, U3.12 (CSN)
unnamed: C24.1, C25.1, R26.1, R27.1, R32.1, U3.4 (VDD), U3.14 (LDO33), U3.58 (AV_DD)
unnamed: C26.1, P3.1, R32.2, U3.3 (TEMPSENSE)
unnamed: C27.1, R33.1, R35.2
unnamed: C32.1, R39.2
unnamed: C33.1, C35.1, C36.1, R38.1, R39.1, R42.2, R43.1, U3.41 (CSNOUT)
unnamed: D1.2 (A), D2.2 (A), R15.1
unnamed: D3.1 (K), R23.2
unnamed: D3.2 (A), R26.2, U3.51 (STATUS), U5.1, W5.1
unnamed: D4.1 (K), R24.2
unnamed: D4.2 (A), R27.2, U3.2 (FAULT), W6.1
unnamed: D5.2 (A), Q6.2 (G), Q7.2 (C), R40.2, W11.1
unnamed: F1.2, R3.1, U2.12 (S), U2.13 (S), U2.14 (S), U2.15 (SP), U2.16 (S), W1.2
unnamed: P5.1, U5.5
unnamed: P5.2, U5.4
unnamed: Q1.1 (D), R9.2, R10.1, U3.54 (VINR)
unnamed: Q1.3 (G), R3.2, R4.1
unnamed: Q3.1 (S), Q3.2 (S), Q3.3 (S), Q5.1 (S), Q5.2 (S), Q5.3 (S), R28.2, R31.2
unnamed: Q6.1 (D), R36.1
unnamed: Q7.1 (B), R30.1, U3.8 (SWEN), U3.49 (SWENO)
unnamed: Q7.3 (E), R41.1
unnamed: R1.2, R2.1, U3.11 (SHDN), W2.1
unnamed: R5.1, U1.2 (PG)
unnamed: R6.1, U2.2 (PG)
unnamed: R7.2, R8.1, R11.1, U3.1 (FBIR), U3.15 (FBIN)
unnamed: R12.2, U3.6 (FBIW)
unnamed: R13.2, U3.22 (RT)
unnamed: R16.1, U3.50 (IOW)
unnamed: R17.1, U3.64 (IOR)
unnamed: R21.1, U3.44 (CSNIN)
unnamed: R22.1, U3.20 (CLKOUT)
unnamed: R25.2, U3.32 (TG1)
unnamed: R33.2, U3.5 (FBOW)
unnamed: R34.2, U3.25 (BG2)
unnamed: R35.1, R36.2, R37.1, U3.16 (FBOUT), U3.57 (FBOR)
unnamed: R43.2, R44.1, U4.1 (V1)
unnamed: R45.2, R46.1, U4.2 (V2), U4.3 (V3)
unnamed: R47.1, U5.2
unnamed: R48.1, U3.21 (SYNC)
unnamed: R49.1, U3.63 (CHARGECFG2)
unnamed: U3.35 (SRVO_FBIN), W10.1
unnamed: U3.36 (SRVO_IIN), W9.1
unnamed: U3.37 (SRVO_IOUT), W8.1
unnamed: U3.38 (SRVO_FBOUT), W7.1
VIN: C2.1, C4.1, C5.1, C9.1, C11.1, C12.1, C14.1, C18.2, C37.1, R1.1, R7.1, R9.1, R20.2, U1.8 (SN), U1.9 (D), U1.10 (D), U1.11 (D), U1.17 (D), U2.8 (SN), U2.9 (D), U2.10 (D), U2.11 (D), U2.17 (D), U3.45 (CSPIN), U3.46 (VIN), W4.1

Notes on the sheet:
Place close to VIN.
CIN1
CIN2
CIN3
COUT3
CCSPOUT
COUT2
COUT1
CIN4
RFBIN1
RFBIN2
RDACI1
RDACI2
CDACI
202kHz
Input Feedback (p.14)
Output Feedback (p. 17)
Input Current Sense (p. 20)
Output Current Sense (p. 20)
Shutdown (p. 27)
Temp Sense (p. 21)
Supply Detection (p.15, p.34)
Voltage, Current, & Temp Sense
I2C addr 0x98
PV_IN: Open Circuit = 17 V Short Circuit = 2.4 A
CHARGING PARAMETERS: Stage 2 Voltage: 33.6 V Maximum Charging Current: 5 A Maximum Trickle Current: 500 mA Switching Frequency: 202 kHz
Feedback Disconnect
Battery Charge Controller w/ MPPT
TODO: label pull-up resistors as no-place?
1% Resistors 75V Capacitors
"Be sure to place all of the filter components (CSX, RSX, CCX) close to the LT8490 for best performance."
3.3V

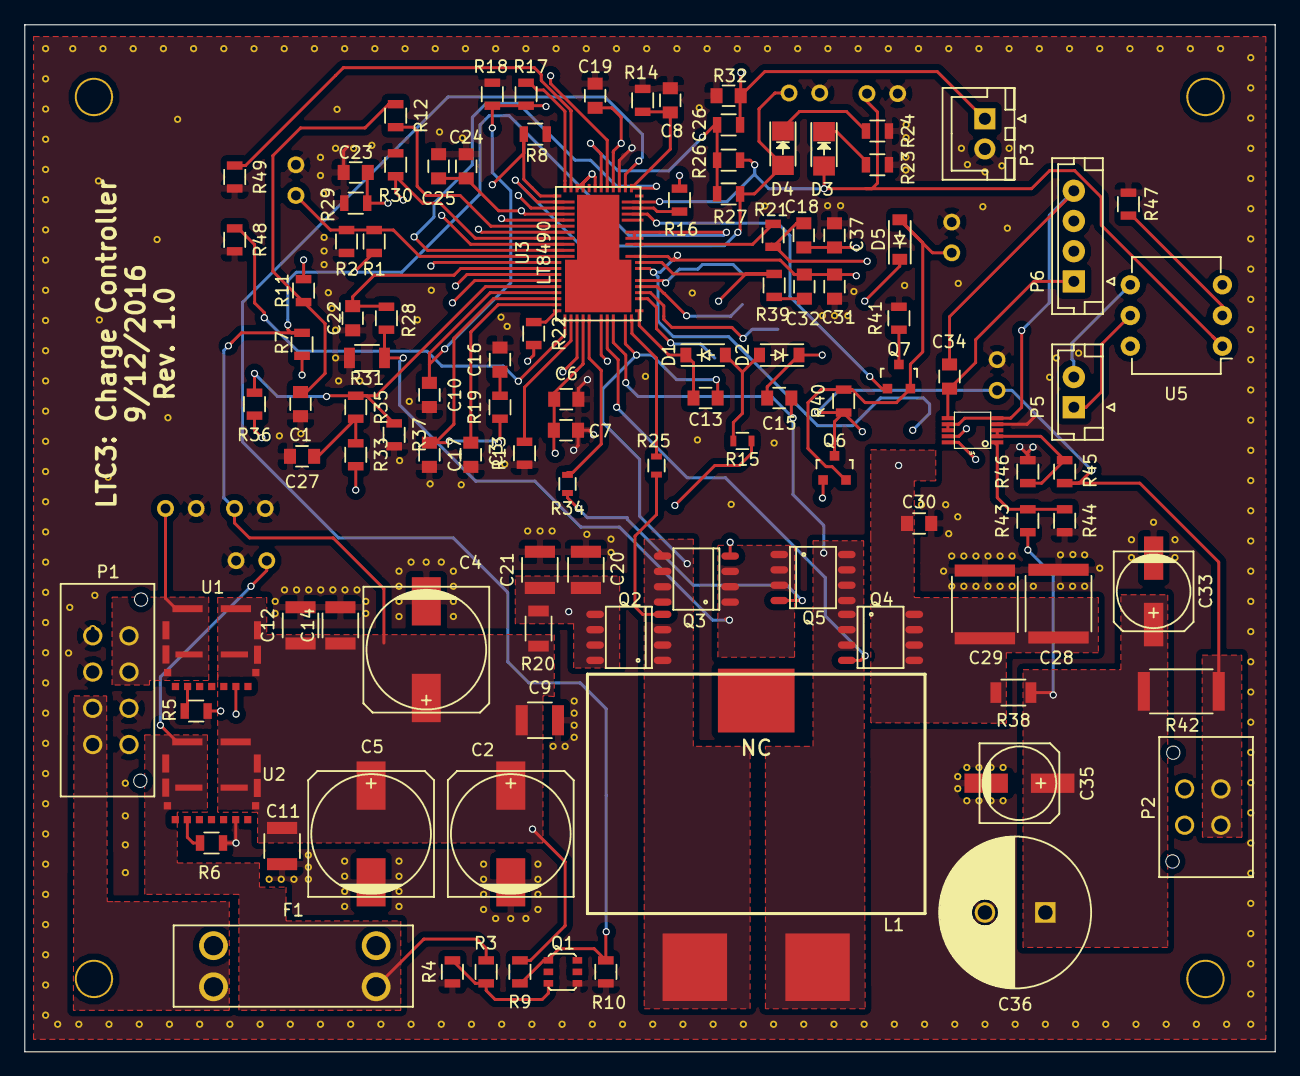
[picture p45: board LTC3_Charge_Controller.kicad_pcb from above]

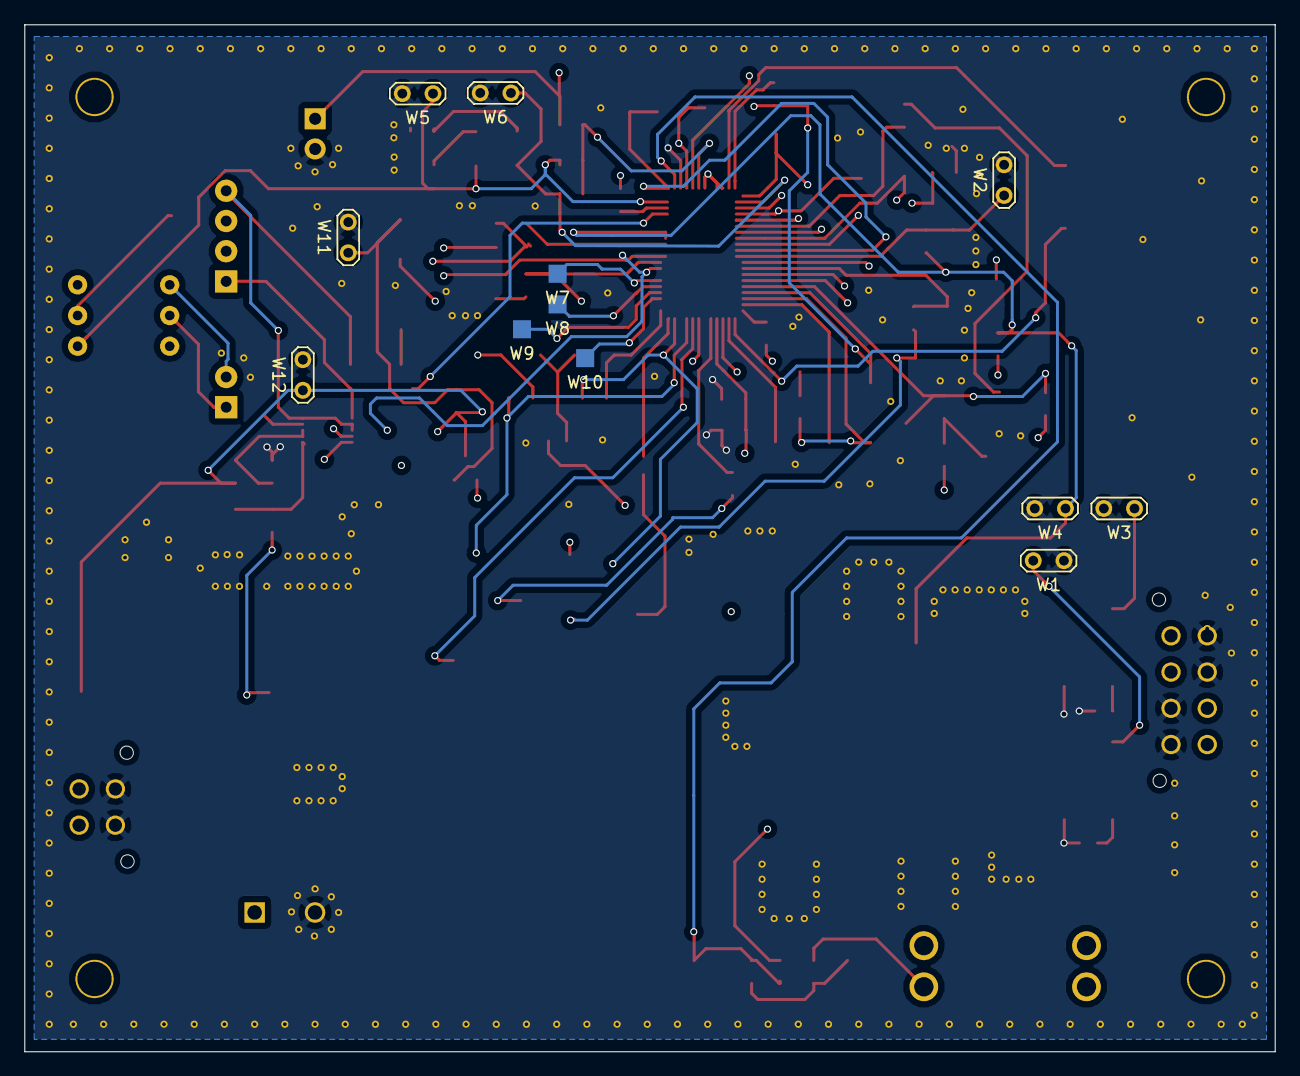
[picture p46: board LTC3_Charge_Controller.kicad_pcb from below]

Board: 4 copper layers, 103.5 x 85.0 mm, 122 parts (12 on the bottom side), 72 nets.

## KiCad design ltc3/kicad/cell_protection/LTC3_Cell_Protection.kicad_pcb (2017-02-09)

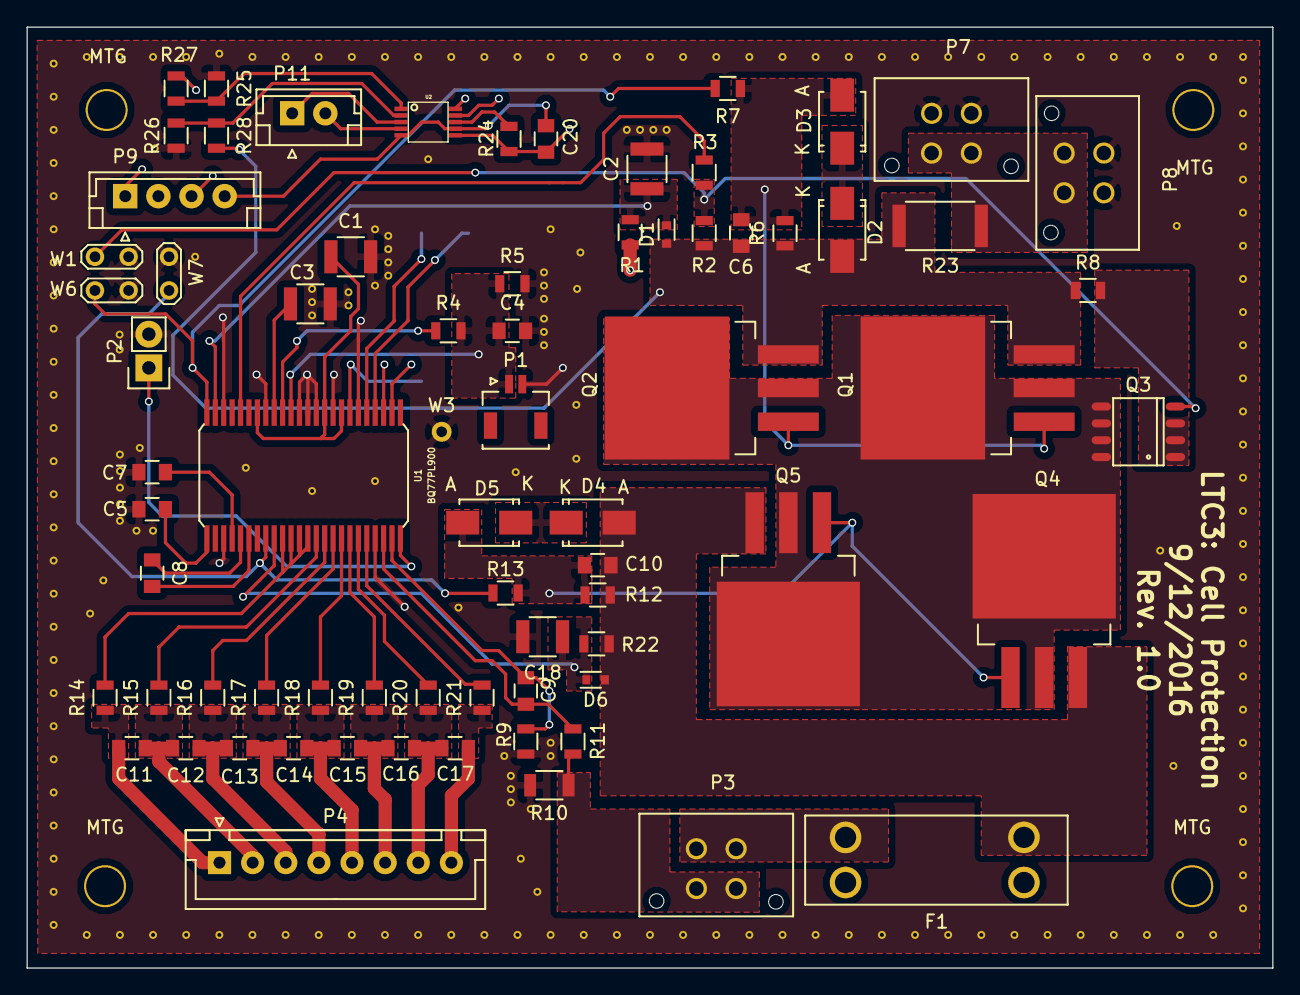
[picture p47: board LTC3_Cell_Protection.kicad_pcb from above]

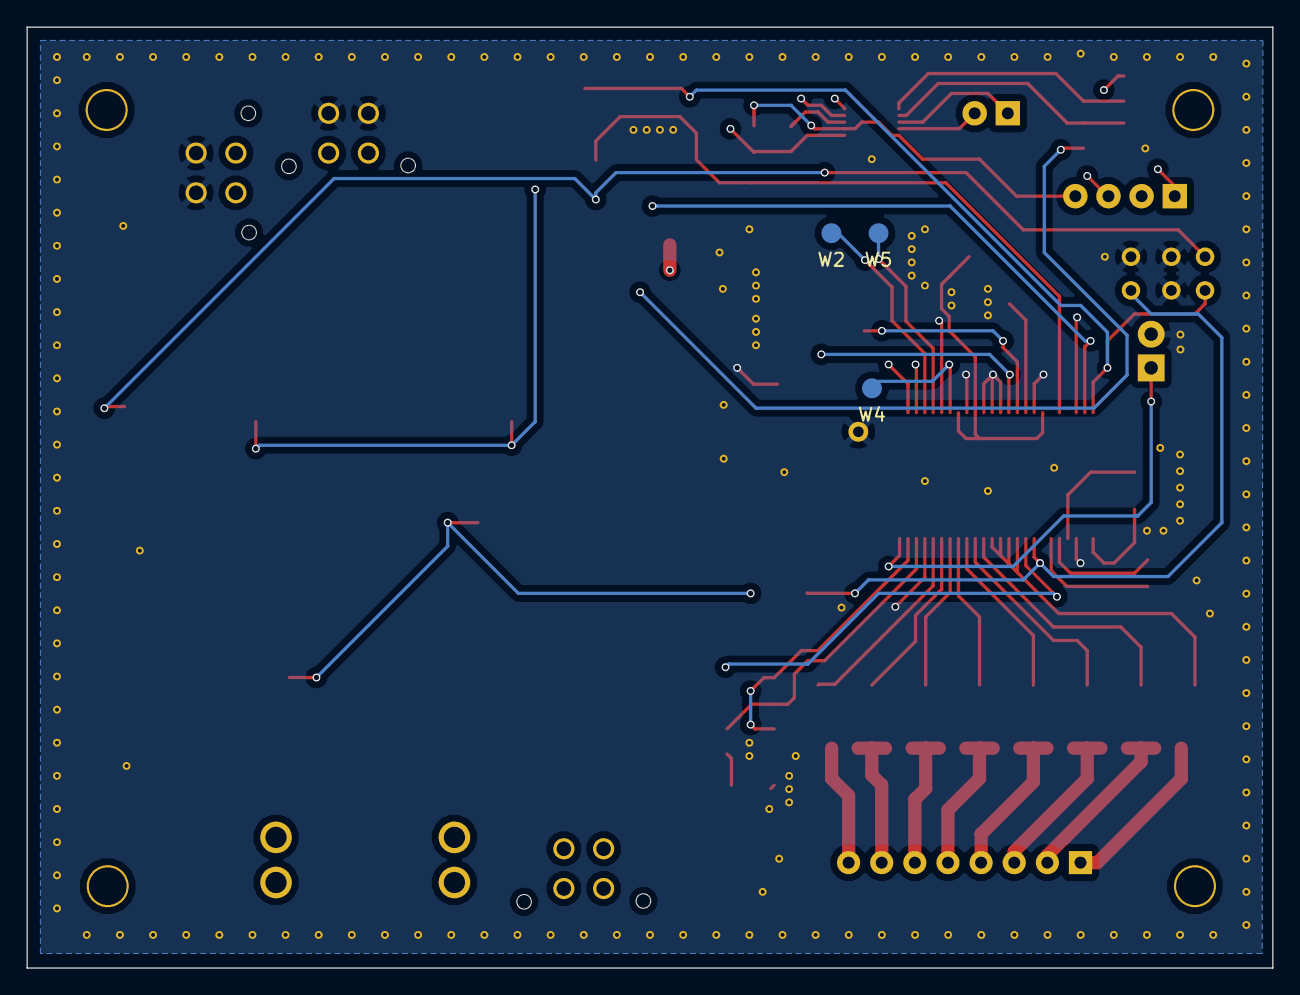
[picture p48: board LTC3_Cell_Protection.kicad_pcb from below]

Board: 4 copper layers, 94.0 x 71.0 mm, 80 parts (3 on the bottom side), 57 nets.

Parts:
C1, C2, C3, C18: 2.2μ; C_1210
C4: 10n; C_0805
C5: 4.7μ; C_0805
C6, C10: 4.7n; C_0805
C7, C8: 1μ; C_0805
C9, C11, C12, C13, C14, C15, C16, C17, C20: 0.1μ; C_0805
D1, D6: CDSU4148; SOD-523
D2, D3, D4, D5: SMAZ16; SMA_Standard
F1: 10A; Fuseholder_Auto_Blade_Regular_Keystone_3557-2
MTG: MountingHole_0.1120in_#4; MountingHole_0.1120in_number4
MTG#2, MTG#3, MTG#4: MountingHole_0.1120in_#4; MountingHole_0.1120in_number4
P1: XH header; JST_SHL_SM02B-SHLS-TF_02x1.00mm_Angled
P2: pin header; Pin_Header_Straight_1x02
P3, P7, P8: XH header; Molex_Microfit3_Header_02x02_Straight_43045-0428
P4: XH header; JST_XH_B08B-XH-A_08x2.50mm_Straight
P9: XH header; JST_EH_B04B-EH-A_04x2.50mm_Straight
P11: XH header; JST_EH_B02B-EH-A_02x2.50mm_Straight
Q1, Q2, Q4, Q5: SUM110P08-11; TO-263-3Lead
Q3: NDS9407; SO-8
R1: 10k; R_0805
R2: 390k; R_0805
R3: 820k; R_0805
R4: 6.98k; R_0805
R5: 61.9k; R_0805
R6, R12: 1M; R_0805
R7, R13: 1k; R_0805
R8: 1.78k; R_0805
R9, R11: 200; R_0805
R10: 1m; R_1206
R14, R15, R16, R17, R18, R19, R20, R21: 510; R_0805
R22: 100k; R_0805
R23: 60m; R_2512
R24: 5.6k; R_0805
R25, R26: 12k; R_0805
R27, R28: 75k; R_0805
U1: BQ77PL900
U2: LTC2990; MSOP-10
W1, W6, W7: TEST; Test_Point_2Pads
W2, W4, W5: TEST_1P; Measurement_Point_Round-SMD-Pad_Small
W3: TEST_1P; Measurement_Point_Round-TH_Small

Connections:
/I2C_CLK: P9.2, U1.27, U2.6
/I2C_DATA: P9.3, U1.26, U2.7
/VBATT: P7.3, P7.4, P8.3, P8.4, R1.1, R23.2, R27.2
GND: C1.2, C2.2, C3.2, C4.2, C5.2, C7.2, C18.2, P1.2, P2.2, P7.1, P7.2, P8.1, P8.2, R5.2, R9.2, R10.1, R25.1, R26.1, U1.3, U1.21, U1.30, U1.33, U1.35, U1.36, U1.37, U1.41, U1.46, W1.2, W3.1, W6.2, W7.2
GNDREF: C20.2, P9.4, U2.5, U2.9
unnamed: C1.1, U1.32, U1.34, U1.42
unnamed: C2.1, D1.1, R1.2, U1.47
unnamed: C3.1, U1.40
unnamed: C4.1, P1.1, R4.2, R5.1, U1.38
unnamed: C5.1, U1.1
unnamed: C6.1, D1.2, D2.2, Q1.3, Q2.3, R2.1, R6.1, R8.1, R23.1, R28.2
unnamed: C6.2, D3.2, Q1.1, Q2.1, R6.2, R7.1
unnamed: C7.1, U1.4
unnamed: C8.1, U1.5
unnamed: C8.2, U1.6
unnamed: C9.1, R9.1, U1.23
unnamed: C9.2, R11.1, U1.22
unnamed: C10.1, D4.2, D6.2, F1.1, Q4.3, Q5.3, R12.1, R22.1
unnamed: C10.2, D5.2, Q4.1, Q5.1, R12.2, R13.1
unnamed: C11.1, P4.1, R14.1
unnamed: C11.2, C12.1, P4.2, R15.1
unnamed: C12.2, C13.1, P4.3, R16.1
unnamed: C13.2, C14.1, P4.4, R17.1
unnamed: C14.2, C15.1, P4.5, R18.1
unnamed: C15.2, C16.1, P4.6, R19.1
unnamed: C16.2, C17.1, P4.7, R20.1
unnamed: C17.2, P4.8, R21.1
unnamed: C18.1, D6.1, R22.2, U1.9
unnamed: C20.1, P9.1, R24.1, U2.10
unnamed: D2.1, D3.1
unnamed: D4.1, D5.1
unnamed: F1.2, P3.1, P3.2
unnamed: P2.1, U1.24
unnamed: P3.3, P3.4, R10.2, R11.2
unnamed: P11.1, U2.3
unnamed: P11.2, U2.4
unnamed: Q1.2, Q1.4, Q2.2, Q2.4, Q3.5, Q3.6, Q3.7, Q3.8, Q4.2, Q4.4, Q5.2, Q5.4
unnamed: Q3.1, Q3.2, Q3.3, R8.2
unnamed: Q3.4, R2.2, R3.1, W1.1
unnamed: R3.2, U1.44
unnamed: R4.1, U1.39
unnamed: R7.2, U1.48, W6.1
unnamed: R13.2, U1.8, W7.1
unnamed: R14.2, U1.10, U1.11, U1.12, U1.13
unnamed: R15.2, U1.14
unnamed: R16.2, U1.15
unnamed: R17.2, U1.16
unnamed: R18.2, U1.17
unnamed: R19.2, U1.18
unnamed: R20.2, U1.19
unnamed: R21.2, U1.20
unnamed: R24.2, U2.8
unnamed: R25.2, R27.1, U2.1
unnamed: R26.2, R28.1, U2.2
unnamed: U1.28, W2.1
unnamed: U1.29, W5.1
unnamed: U1.31, W4.1

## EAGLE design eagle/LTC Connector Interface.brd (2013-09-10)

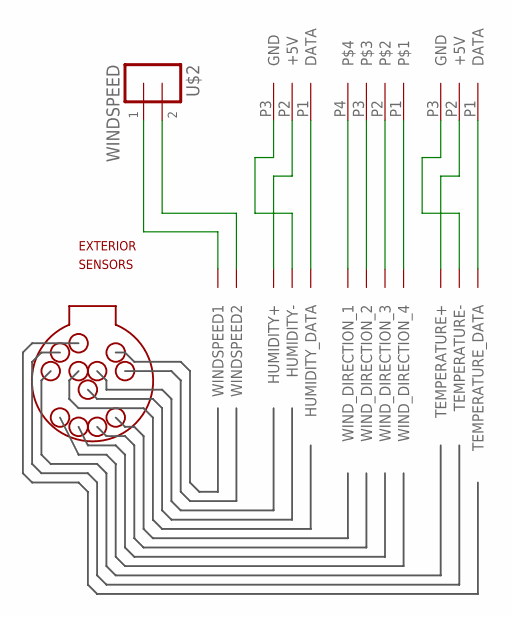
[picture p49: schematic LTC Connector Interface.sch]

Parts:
HUMIDITY: MOLEX-3
TEMP: MOLEX-3
U$1: LAYOUT-LEMO-12PIN; LEMO-12
U$2: WINDSPEED; SCREW-TERM-5MM
WINDDIRECTION: MOLEX-4

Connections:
unnamed: U$1.P6 (WINDSPEED1), U$2.1
unnamed: U$1.P5 (WINDSPEED2), U$2.2
unnamed: U$1.P3 (WIND_DIRECTION_3), WINDDIRECTION.P2
unnamed: U$1.P10 (WIND_DIRECTION_2), WINDDIRECTION.P3
unnamed: U$1.P11 (WIND_DIRECTION_1), WINDDIRECTION.P4
unnamed: U$1.P4 (WIND_DIRECTION_4), WINDDIRECTION.P1
unnamed: TEMP.P1 (DATA), U$1.P1 (TEMPERATURE_DATA)
unnamed: TEMP.P3 (GND), U$1.P8 (TEMPERATURE-)
unnamed: TEMP.P2 (+5V), U$1.P7 (TEMPERATURE+)
unnamed: HUMIDITY.P1 (DATA), U$1.P2 (HUMIDITY_DATA)
unnamed: HUMIDITY.P2 (+5V), U$1.P12 (HUMIDITY+)
unnamed: HUMIDITY.P3 (GND), U$1.P9 (HUMIDITY-)

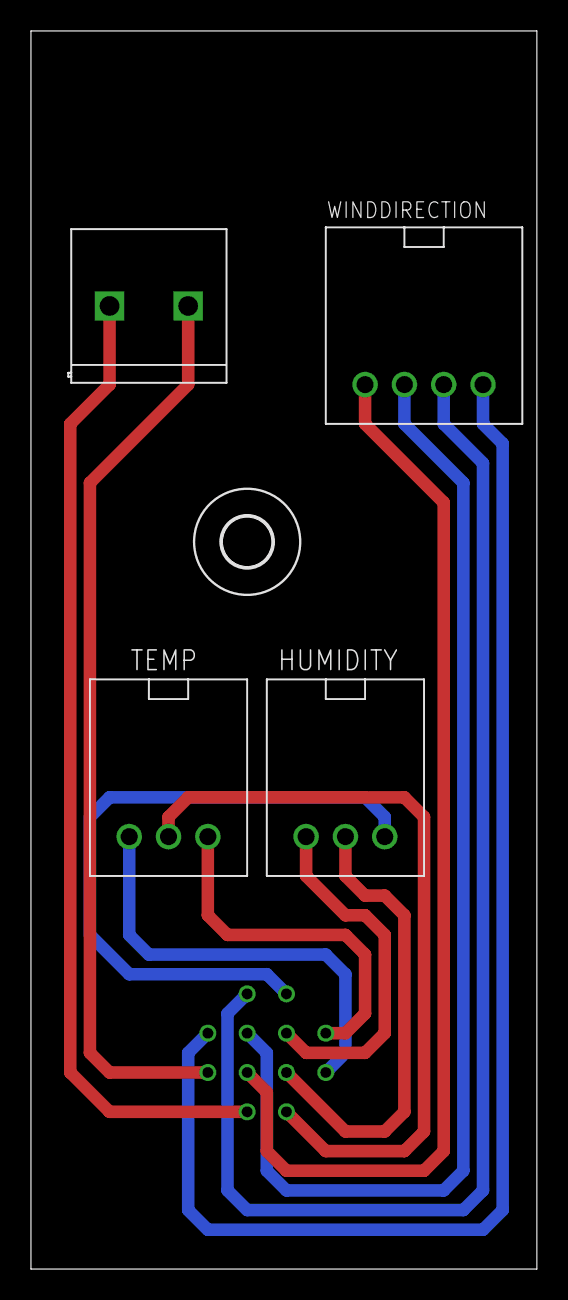
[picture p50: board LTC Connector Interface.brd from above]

Board: 2 copper layers, 32.7 x 80.0 mm, 6 parts (0 on the bottom side), 12 nets.

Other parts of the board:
U$3: 3,2

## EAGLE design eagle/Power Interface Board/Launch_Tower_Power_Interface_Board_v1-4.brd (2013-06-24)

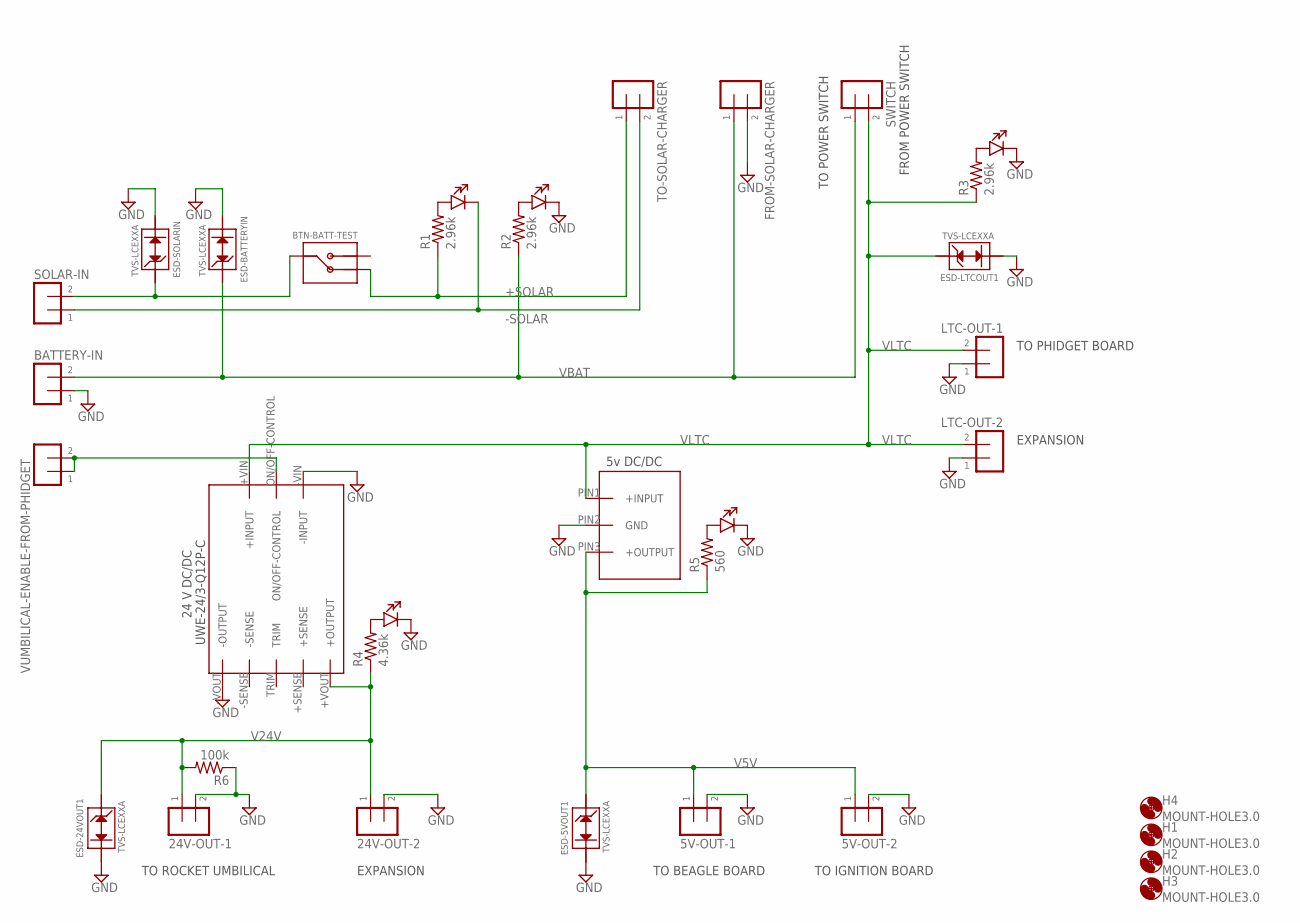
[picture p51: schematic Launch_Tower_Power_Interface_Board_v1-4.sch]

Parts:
5V-OUT-1, 5V-OUT-2, 24V-OUT-1, 24V-OUT-2: SCREW-TERMINAL-5MM; SCREW-TERM-5MM
BATTERY-IN: SCREW-TERMINAL-5MM; SCREW-TERM-5MM
BTN-BATT-TEST: BUTTON-107-3006-EVX; BUTTON-1
DC1: DC/DC_CONV_5V; OKI-SIP
DC2: UWE-24/3-Q12P-C; UWE
ESD-5VOUT1, ESD-24VOUT1: TVS-LCEXXA; D0-201
ESD-BATTERYIN: TVS-LCEXXA; D0-201
ESD-LTCOUT1: TVS-LCEXXA; D0-201
ESD-SOLARIN: TVS-LCEXXA; D0-201
FROM-SOLAR-CHARGER: SCREW-TERMINAL-5MM; SCREW-TERM-5MM
H1, H2, H3, H4: MOUNT-HOLE3.0; 3,0
LED-5V-DC/DC, LED-24V-DC/DC: LED-550-XX04; LED-550
LED-BATTERY-IN: LED-550-XX04; LED-550
LED-SOLAR-IN: LED-550-XX04; LED-550
LED-SWITCH-IN: LED-550-XX04; LED-550
LTC-OUT-1, LTC-OUT-2: SCREW-TERMINAL-5MM; SCREW-TERM-5MM
R1, R2, R3: 2.96k; 0805-B
R4: 4.36k; 0805-B
R5: 560; 0805-B
R6: 100k; 0805-B
SOLAR-IN: SCREW-TERMINAL-5MM; SCREW-TERM-5MM
SWITCH: SCREW-TERMINAL-5MM; SCREW-TERM-5MM
TO-SOLAR-CHARGER: SCREW-TERMINAL-5MM; SCREW-TERM-5MM
VUMBILICAL-ENABLE-FROM-PHIDGET: SCREW-TERMINAL-5MM; SCREW-TERM-5MM

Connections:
+SOLAR: BTN-BATT-TEST.NC, R1.1, TO-SOLAR-CHARGER.1
-SOLAR: LED-SOLAR-IN.CATHODE, SOLAR-IN.1, TO-SOLAR-CHARGER.2
GND: 5V-OUT-1.2, 5V-OUT-2.2, 24V-OUT-1.2, 24V-OUT-2.2, BATTERY-IN.1, DC1.PIN2 (GND), DC2.-VIN (-INPUT), DC2.-VOUT (-OUTPUT), ESD-5VOUT1.CATHODE, ESD-24VOUT1.CATHODE, ESD-BATTERYIN.CATHODE, ESD-LTCOUT1.CATHODE, ESD-SOLARIN.CATHODE, FROM-SOLAR-CHARGER.2, LED-5V-DC/DC.CATHODE, LED-24V-DC/DC.CATHODE, LED-BATTERY-IN.CATHODE, LED-SWITCH-IN.CATHODE, LTC-OUT-1.1, LTC-OUT-2.1, R6.1
GPIO: DC2.ON/OFF-CONTROL, VUMBILICAL-ENABLE-FROM-PHIDGET.1, VUMBILICAL-ENABLE-FROM-PHIDGET.2
unnamed: LED-SOLAR-IN.ANODE, R1.2
unnamed: LED-BATTERY-IN.ANODE, R2.2
unnamed: LED-SWITCH-IN.ANODE, R3.2
unnamed: LED-5V-DC/DC.ANODE, R5.2
unnamed: LED-24V-DC/DC.ANODE, R4.2
unnamed: BTN-BATT-TEST.COMMON, ESD-SOLARIN.ANODE, SOLAR-IN.2
V5V: 5V-OUT-1.1, 5V-OUT-2.1, DC1.PIN3 (+OUTPUT), ESD-5VOUT1.ANODE, R5.1
V24V: 24V-OUT-1.1, 24V-OUT-2.1, DC2.+VOUT (+OUTPUT), ESD-24VOUT1.ANODE, R4.1, R6.2
VBAT: BATTERY-IN.2, ESD-BATTERYIN.ANODE, FROM-SOLAR-CHARGER.1, R2.1, SWITCH.1
VLTC: DC1.PIN1 (+INPUT), DC2.+VIN (+INPUT), ESD-LTCOUT1.ANODE, LTC-OUT-1.2, LTC-OUT-2.2, R3.1, SWITCH.2

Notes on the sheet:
5v DC/DC
TO POWER SWITCH
FROM POWER SWITCH
EXPANSION
TO PHIDGET BOARD
TO BEAGLE BOARD
TO IGNITION BOARD
UWE-24/3-Q12P-C
TO ROCKET UMBILICAL
24 V DC/DC

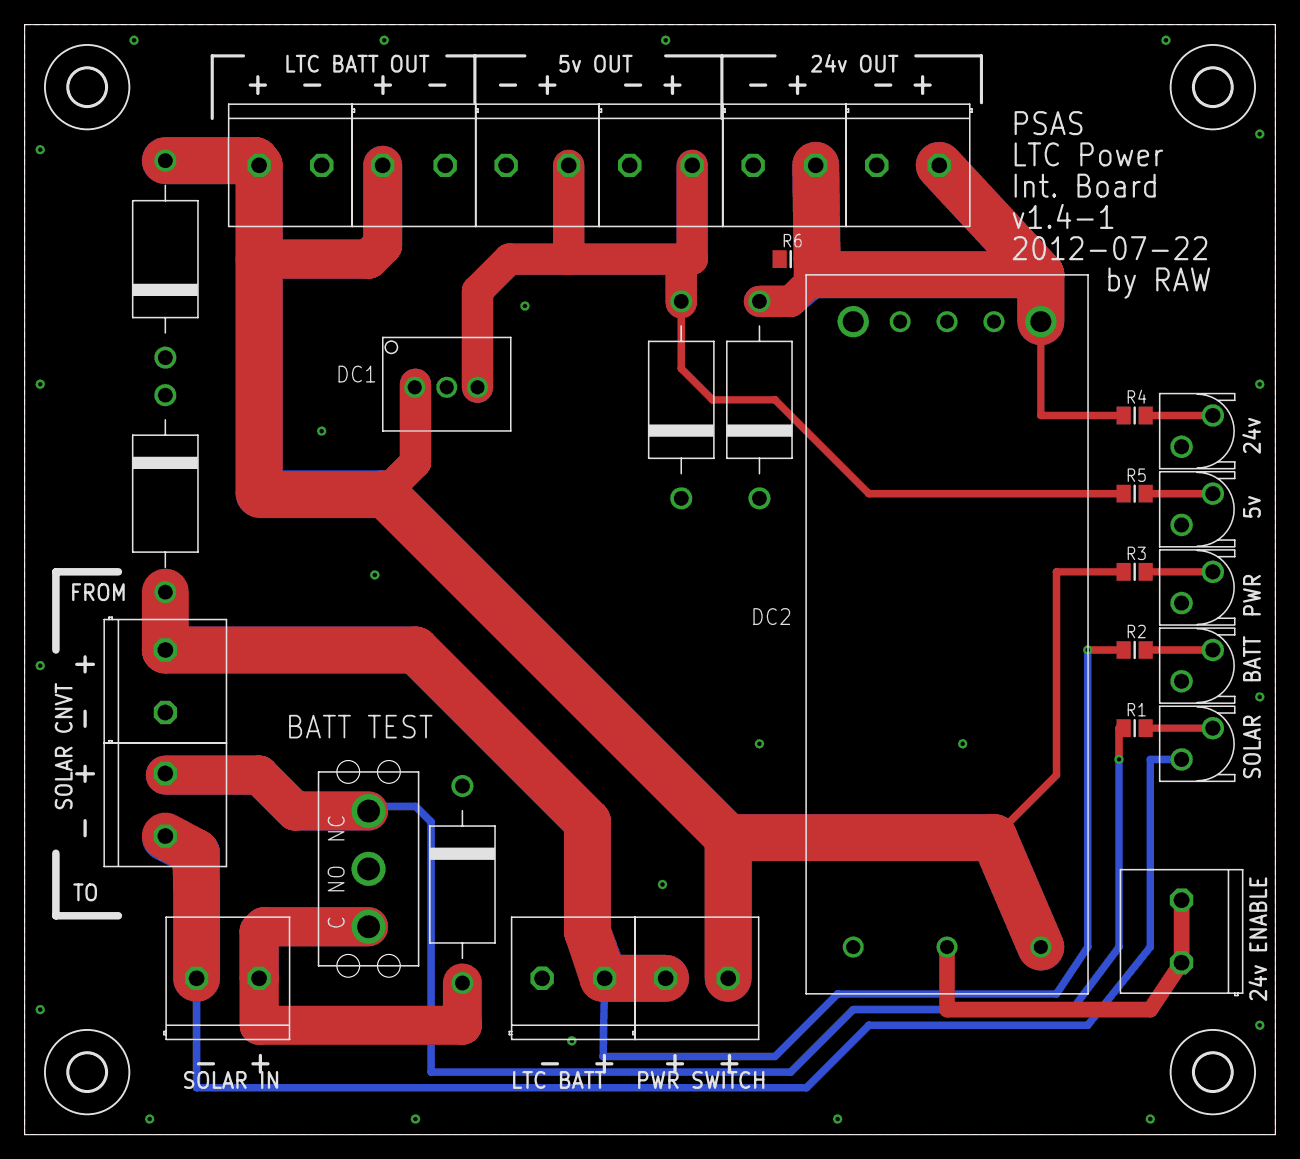
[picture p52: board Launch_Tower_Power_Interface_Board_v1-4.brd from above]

Board: 2 copper layers, 101.6 x 90.2 mm, 35 parts (0 on the bottom side), 14 nets.

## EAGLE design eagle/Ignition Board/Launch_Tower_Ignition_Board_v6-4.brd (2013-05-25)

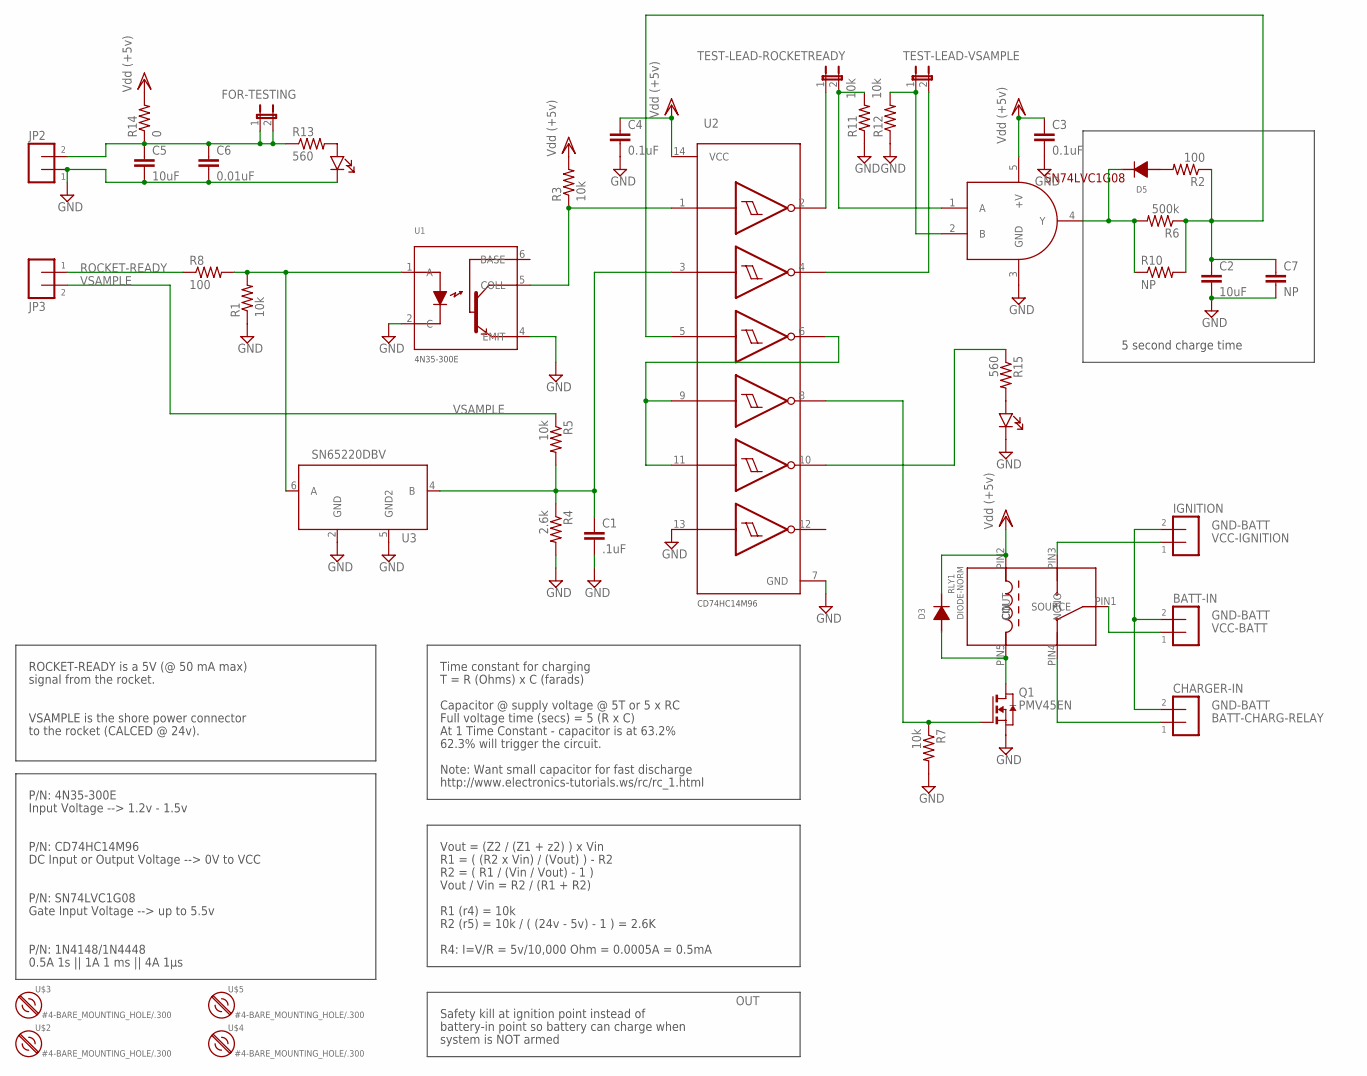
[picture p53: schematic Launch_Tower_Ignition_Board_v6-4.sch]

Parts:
BATT-IN: SCREW-TERMINAL-5MM; SCREW-TERM-5MM
C1: .1uF; 0805-B
C2, C5: 10uF; 0805-B
C3, C4: 0.1uF; 0805-B
C6: 0.01uF; 0805-B
C7: NP; CAP-PTH-SMALL
CHARGER-IN: SCREW-TERMINAL-5MM; SCREW-TERM-5MM
D3, D5: DIODE-NORM; DIODE
FOR-TESTING: JUMPER-2PTH; 1X02
IGNITION: SCREW-TERMINAL-5MM; SCREW-TERM-5MM
JP2, JP3: SCREW-TERMINAL-5MM; SCREW-TERM-5MM
LED-POWER-INDICATOR, LED-POWER-INDICATOR1: LED-550-XX04; LED-550
Q1: PMV45EN; SOT23
R1, R3, R5, R7, R11, R12: 10k; 0805-B
R2, R8: 100; 0805-B
R4: 2.6k; 0805-B
R6: 500k; 0805-B
R10: NP; 0207/10
R13, R15: 560; 0805-B
R14: 0; 0805-B
RLY1: RELAY-2; G5LA
TEST-LEAD-ROCKETREADY: JUMPER-2PTH; 1X02
TEST-LEAD-VSAMPLE: JUMPER-2PTH; 1X02
U1: OPTOISOLATOR; 4N35-300E
U2: INVERT GATES; INVERTSOIC14
U3: SN65220DBV; SOT23-6L
U4: AND GATE; SOT23-5
U$2, U$3, U$4, U$5: #4-BARE_MOUNTING_HOLE/.300; #4/.300-BARE+STD_NUT_OR_STAR_WASHER

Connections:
BATT-CHARG-RELAY: CHARGER-IN.1, RLY1.PIN4 (NC)
GND-BATT: BATT-IN.2, CHARGER-IN.2, IGNITION.2
unnamed: R12.2, TEST-LEAD-VSAMPLE.1, U4.2 (B)
unnamed: LED-POWER-INDICATOR.ANODE, R13.2
unnamed: R3.1, U1.5 (COLL), U2.1 (1A)
unnamed: JP3.1, R8.1
unnamed: R11.2, TEST-LEAD-ROCKETREADY.2, U4.1 (A)
unnamed: TEST-LEAD-VSAMPLE.2, U2.4 (2Y)
unnamed: C1.1, R4.1, R5.2, U2.3 (2A), U3.4 (B)
unnamed: D5.A, R2.2
unnamed: D3.A, Q1.3 (D), RLY1.PIN5 (CIN)
unnamed: Q1.1 (G), R7.1, U2.8 (4Y)
unnamed: TEST-LEAD-ROCKETREADY.1, U2.2 (1Y)
unnamed: C5.1, C6.1, FOR-TESTING.1, FOR-TESTING.2, JP2.2, R13.1, R14.1
unnamed: D5.C, R6.2, R10.1, U4.4 (Y)
unnamed: R15.1, U2.10 (5Y)
unnamed: C2.1, C7.1, R2.1, R6.1, R10.2, U2.5 (3A)
unnamed: LED-POWER-INDICATOR1.ANODE, R15.2
N-NOT2: U2.6 (3Y), U2.9 (4A), U2.11 (5A)
NAME: C1.2, C2.2, C3.2, C4.2, C5.2, C6.2, C7.2, JP2.1, LED-POWER-INDICATOR.CATHODE, LED-POWER-INDICATOR1.CATHODE, Q1.2 (S), R1.1, R4.2, R7.2, R11.1, R12.1, U1.2 (C), U1.4 (EMIT), U2.7 (GND), U2.13 (6A), U3.2 (GND), U3.5 (GND2), U4.3 (GND)
ROCKET-READY: R1.2, R8.2, U1.1 (A), U3.6 (A)
VCC-BATT: BATT-IN.1, RLY1.PIN1 (SOURCE)
VCC-IGNITION: IGNITION.1, RLY1.PIN3 (NO)
VDD: C3.1, C4.1, D3.C, R3.2, R14.2, RLY1.PIN2 (COUT), U2.14 (VCC), U4.5 (+V)
VSAMPLE: JP3.2, R5.1

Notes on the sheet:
ROCKET-READY is a 5V (@ 50 mA max)
signal from the rocket.
VSAMPLE is the shore power connector
to the rocket (CALCED @ 24v).
OUT
R4: I=V/R = 5v/10,000 Ohm = 0.0005A = 0.5mA
Time constant for charging
T = R (Ohms) x C (farads)
Capacitor @ supply voltage @ 5T or 5 x RC
Full voltage time (secs) = 5 (R x C)
Note: Want small capacitor for fast discharge
Vout = (Z2 / (Z1 + z2) ) x Vin
R1 = ( (R2 x Vin) / (Vout) ) - R2
R2 = ( R1 / (Vin / Vout) - 1 )
Vout / Vin = R2 / (R1 + R2)
0.5A 1s || 1A 1 ms || 4A 1μs
R1 (r4) = 10k
Gate Input Voltage --> up to 5.5v
DC Input or Output Voltage --> 0V to VCC
P/N: SN74LVC1G08
P/N: CD74HC14M96
P/N: 4N35-300E
Input Voltage --> 1.2v - 1.5v
R2 (r5) = 10k / ( (24v - 5v) - 1 ) = 2.6K
P/N: 1N4148/1N4448
http://www.electronics-tutorials.ws/rc/rc_1.html
5 second charge time
Safety kill at ignition point instead of
battery-in point so battery can charge when
system is NOT armed
At 1 Time Constant - capacitor is at 63.2%
62.3% will trigger the circuit.


Board: 2 copper layers, 87.6 x 69.8 mm, 43 parts (0 on the bottom side), 25 nets.

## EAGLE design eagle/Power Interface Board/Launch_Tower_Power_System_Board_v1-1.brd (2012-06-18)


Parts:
5V-OUT-1, 5V-OUT-2: M023.5MM; SCREWTERMINAL-3.5MM-2
19V-DC/DC-IN, 19V-OUT-1, 19V-OUT-2: M025MM; SCREWTERMINAL-5MM-2
BATTERY-IN: M025MM; SCREWTERMINAL-5MM-2
DC1: NME
FROM-SOLAR-CONVERTOR: M025MM; SCREWTERMINAL-5MM-2
H1, H2, H3, H4: MOUNT-HOLE3.0; 3,0
JP1, JP2: JUMPER-2PTH; 1X02
LED-5V-DC/DC-IN, LED-19V-DC/DC-IN: LTE-302
LED-BATTERY-IN: LTE-302
LED-RELAY-IN, LED-RELAY-IN1: LTE-302
LED-SOLAR-IN: LTE-302
LED-SWITCH-IN: LTE-302
LTC-OUT: M025MM; SCREWTERMINAL-5MM-2
R1, R2, R3, R4, R7, R8, R9: RESISTORPTH-1/2W; AXIAL-0.5
RELAY-19V-1, RELAY-19V-2: M025MM; SCREWTERMINAL-5MM-2
SOLAR-IN: M025MM; SCREWTERMINAL-5MM-2
SWITCH: M025MM; SCREWTERMINAL-5MM-2
TO-19V-DC/DC: M025MM; SCREWTERMINAL-5MM-2
TO-SOLAR-CONVERTOR: M025MM; SCREWTERMINAL-5MM-2

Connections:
GND: 5V-OUT-1.2, 5V-OUT-2.2, 19V-DC/DC-IN.1, 19V-OUT-1.2, 19V-OUT-2.2, BATTERY-IN.1, DC1.1 (-VIN), DC1.3 (-VOUT), FROM-SOLAR-CONVERTOR.2, LED-5V-DC/DC-IN.C, LED-19V-DC/DC-IN.C, LED-BATTERY-IN.C, LED-RELAY-IN.C, LED-RELAY-IN1.C, LED-SWITCH-IN.C, LTC-OUT.1, TO-19V-DC/DC.2
unnamed: LED-SOLAR-IN.A, R1.P$2 (2)
unnamed: 19V-OUT-2.1, JP2.2, R4.P$1 (1), RELAY-19V-2.1
unnamed: 19V-OUT-1.1, JP1.2, R3.P$1 (1), RELAY-19V-1.1
unnamed: LED-SWITCH-IN.A, R2.P$2 (2)
unnamed: LED-RELAY-IN.A, R3.P$2 (2)
unnamed: BATTERY-IN.2, FROM-SOLAR-CONVERTOR.1, R7.P$1 (1), SWITCH.1
unnamed: LED-BATTERY-IN.A, R7.P$2 (2)
unnamed: LED-5V-DC/DC-IN.A, R8.P$2 (2)
unnamed: LED-RELAY-IN1.A, R4.P$2 (2)
unnamed: LED-19V-DC/DC-IN.A, R9.P$2 (2)
unnamed: LED-SOLAR-IN.C, SOLAR-IN.1, TO-SOLAR-CONVERTOR.2
unnamed: 19V-DC/DC-IN.2, JP1.1, JP2.1, R9.P$1 (1), RELAY-19V-1.2, RELAY-19V-2.2
unnamed: R1.P$1 (1), SOLAR-IN.2, TO-SOLAR-CONVERTOR.1
unnamed: 5V-OUT-1.1, 5V-OUT-2.1, DC1.4 (+VOUT), R8.P$1 (1)
unnamed: DC1.2 (+VIN), LTC-OUT.2, R2.P$1 (1), SWITCH.2, TO-19V-DC/DC.1

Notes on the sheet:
Solar IN
Battery IN
19v DC/DC IN
5v DC/DC IN
TO 19v DC/DC
TO RELAY
TO POWER SWITCH
FROM POWER SWITCH
TO SOLAR CONVERTOR
FROM SOLAR CONVERTOR
FROM RELAY
5v OUT
19v OUT
LTC out


Board: 2 copper layers, 105.1 x 71.1 mm, 35 parts (0 on the bottom side), 16 nets.

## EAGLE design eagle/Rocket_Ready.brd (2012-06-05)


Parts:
C1, C2: C-EU0805-B-NOSILK; 0805-B-NOSILK
D5, D6: DIODEPTH; DIODE-1N4001
IC1: INVERT GATES; INVERTSOIC14
IC2: OPTOISOLATOR; 4N35-300E
JP1: 5MM screw; SCREWTERMINAL-5MM-2
JP2, JP3: 3.5MM screw; SCREWTERMINAL-3.5MM-2
L1: RELAY; G5T-1A
Q1: NMOSFET; FETSO-8
R1, R2, R3, R4, R5, R6, R7: R-US_0805-B-NOSILK; 0805-B-NOSILK
U$1: AND GATE; SOT23-5
ZD1, ZD2: DIODE-ZENERPTH; DIODE-ZENER

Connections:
GND: C1.2, C2.2, IC1.7 (GND), IC2.2 (C), IC2.4 (EMIT), JP2.1, Q1.1 (SOURCE), R1.1, R4.1, R7.1, U$1.3 (GND), ZD2.P$2 (A)
unnamed: IC1.4 (2Y), U$1.2 (B)
unnamed: D5.C, R6.2, U$1.4 (Y)
unnamed: IC1.1 (1A), IC2.5 (COLL), R3.1
unnamed: IC1.2 (1Y), U$1.1 (A)
unnamed: IC2.1 (A), R2.1
unnamed: C1.1, IC1.3 (2A), R4.2, R5.1
unnamed: R1.2, R2.2, ZD1.P$1 (C), ZD2.P$1 (C)
unnamed: D6.A, L1.CIN, Q1.5 (DRAIN)
unnamed: IC1.8 (4Y), Q1.4 (GATE), R7.2
unnamed: D6.C, IC1.14 (VCC), JP2.2, L1.COUT, R3.2, U$1.5 (+V)
N-NOT1: C2.1, D5.A, IC1.5 (3A), R6.1
N-NOT2: IC1.6 (3Y), IC1.9 (4A)
VFIRE-IN: JP1.2, L1.SW2
VFIRE-OUT: JP1.1, L1.SW1
VROCKET: JP3.1, ZD1.P$2 (A)
VSAMPLE: JP3.2, R5.2


Board: 2 copper layers, 100.0 x 35.5 mm, 21 parts (0 on the bottom side), 17 nets.

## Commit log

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2012-06-18 Pushed latest ignition board, power board, and updated launch-tower library files. Also changed directory structure.
    [Ignition_Board.brd, Ignition_Board.sch, Launch_Tower_Power_System_Board_v1-1.brd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]
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2012-07-21 Latest versions checked against physical parts. Changes to all boards and library to make adustments. Also uploaded data sheets for parts.
    [Launch_Tower_Ignition_Board_v6-4.brd, Launch_Tower_Ignition_Board_v6-4.sch, Launch_Tower_Power_Interface_Board_v1-4.brd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]
2012-07-23 Minor changes to Ignition board and library - smaller diode Signed-off-by: richard <richard@mailwh.com>
    [Launch_Tower_Ignition_Board_v6-4.brd, Launch_Tower_Ignition_Board_v6-4.sch]
2012-07-23 Clean up of power distribution board, lots of small changes, including rcl_custom 0805 packages, ERC and DRC issues, cleaned up tnames, etc.
    [Launch_Tower_Power_Interface_Board_v1-1.brd, Launch_Tower_Power_Interface_Board_v1-1.sch, Launch_Tower_Power_Interface_Board_v1-2.brd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]
2012-07-23 Cleaned up ignition board for manufacturing - ERCs, DRCs, flood fills, switched MOSFET to have a higher Vgs on, added LED for the ignition on circuit, cleaned up tsilk layer.
    [Launch_Tower_Ignition_Board_v5-0.brd, Launch_Tower_Ignition_Board_v5-0.sch, Launch_Tower_Ignition_Board_v6-0.brd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]
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2013-03-05 Additional Repo files from Richard's local
    Adding lasercut files for LTC, additional Eagle files, and
    presentations.
    [1014_2.step, 1124_0.step, BEAGLE-xM_BOM_REVC.xls]
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2014-08-01 Substantial repo clean-up. 1. Moved quite a bit of documentation (PSAS and third party) from the "launch-tower-comm" repo, as it really belongs here with the computer-related files. 2. Rearranged a f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
    [InterfaceKit-simple.sdf, shape.obj, teapot.obj]
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2014-12-03 Updated LV2 system schematic to include DC-DC adapter and extra relay connections.
    [LTC Whole System Schematic.sch]
2015-01-05 Deleted LTC3 whiteboard snapshots. Created a new issue and attached them to it.
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2015-04-02 More work on LTC3 schematic. 1. Created placeholder "power in" schematic. 2. First cut at external trigger schematic (MOSTFETs and mechanical relays).
    [BBB_Cape.sch, Launch_Tower_Computer_III.sch, beaglebone_cape.sch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]
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2015-04-02 Fixed mistakes in triggers schematic; misc. clean-up.
    [Launch_Tower_Computer_III.sch, dcdc_converter_19v.sch, dcdc_converter_5v.sch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]
2015-04-03 Fixed incorrect FET symbol on LTC3 ext. triggers schematic.
    [Launch_Tower_Computer_III.sch, beaglebone_cape.sch, dcdc_converter_19v.sch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]
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2015-04-08 More progress on LTC3 schematic. Finished first draft of external device support (power and triggers). Added a few new datasheets.
    [Launch_Tower_Computer_III.sch, beaglebone_cape.sch, dcdc_converter_19v.sch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]
2015-04-09 Updated design spec; schematic. Completed "External Device Support" section of design spec. Replaced fuses with PTC devices in external device support schematic.
    [external_device_support.sch]
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2015-04-18 Modified LTC3 external device support schematics. 1. Split single sheet into separate power and trigger sheets. 2. Added current-limiting resistor to LED input pin on each photorelay. 3. Added bleed 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
    [Launch_Tower_Computer_III.sch, beaglebone_cape.sch, dcdc_converter_19v.sch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]
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2015-04-21 LTC3 Design Spec updates. 1. Changed 5 V DC-DC convert from Cincon to TDK-Lambda. The Cincon is no longer in stock at Mouser, and lead times are ridiculous. 2. Cleaned up the "Power" section. 3. Re-w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
2015-05-20 LTC3 KiCad updates. 1. Modified schematics to play nicely with (relatively) recent changes in KiCad's stock component libraries (e.g., redrawn capacitor and resistor symbols). 2. Began work on PTN780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
    [Launch_Tower_Computer_III.sch, beaglebone_cape.sch, dcdc_converter_19v.sch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]
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2015-06-10 Fixing bad stuff.
    [Charging_Circuit.sch]
2015-06-13 Fixed annoying obsolete library component warning (again). Had to delete the -cache.lib file.
    [Launch_Tower_Computer_III.sch, beaglebone_cape.sch, dcdc_converter_19v.sch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]
2015-06-13 More LTC3 schematic clean-up. 1. Prettified the Cape EEPROM schematic. 2. More contstantly-changing-KiCad-library-related fixes, this time to the power and trigger relay schematics.
    [Launch_Tower_Computer_III.sch, beaglebone_cape.sch, dcdc_converter_19v.sch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]
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2015-06-13 Fixed incorrect NMOSFET symbol in external power and trigger schematics. Pin numbering order on symbol did not match that of part footprint.
    [external_power.sch, external_triggers.sch]
2015-06-13 LTC3 DC-DC converter schematic corrections. 1. Corrected DC-DC converter symbol on 19 VDC rail. 2. Merged separate converter schematics into one.
    [Launch_Tower_Computer_III.sch, beaglebone_cape.sch, external_power.sch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]
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2015-07-01 LTC3 design progress: added 12V DC-DC converter; prettified top-level schematic. Requirements Spec calls for 12VDC external power. Batteries are now 28.8VDC (nominal), so we'll need a third converter.
    [Launch_Tower_Computer_III.sch, beaglebone_cape.sch, dcdc_converter.sch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]
2015-07-01 More LTC3 design: completed DC-DC converter schematics. Mostly. A thorough review of the PTN78020[WH] datasheet followed by a once-over of the schematic wouldn't hurt.
    [Launch_Tower_Computer_III.sch, beaglebone_cape.sch, dcdc_converter.sch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]
2015-07-02 Minor adjustments to LTC3 DC-DC converter schematics. Fixed the V_out sense lines; added a few helpful notes.
    [dcdc_converter.sch]
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2015-07-23 More work on power sensors. Beginning to wire up the DC-DC Converter sheet with the BeagleBone Cape sheet.
    [Launch_Tower_Computer_III.sch, beaglebone_cape.sch, dcdc_converter.sch]
2015-07-24 Moved voltage/current sense resistors onto DC-DC Converter sheet. From the BeagleBone Cape sheet. This makes the schematics cleaner, as there are fewer hierarchical pins to keep track of.
    [Launch_Tower_Computer_III.sch, beaglebone_cape.sch, dcdc_converter.sch]
2015-08-02 Completed first draft of power and temperature sensors.
    Updated the design spec accordingly. Also renamed "Power In" sheet to
    "Power Sources".
    [Launch_Tower_Computer_III.sch, beaglebone_cape.sch, dcdc_converter.sch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]
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2015-08-14 Deleted charging circuit KiCad files.
    Inadvertently merged in from the Charging_Circuit branch. Not even
    close to ready for prime time.
    [Charging_Circuit.sch]
2015-09-02 Replaced BBB expansion header symbols Drew new symbols with more detail. All pins are now named. Note that the BBB has upwards of seven functions per pin. Not all functions are included in each pin's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
    [Launch_Tower_Computer_III.sch, beaglebone_cape.sch, dcdc_converter.sch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]
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2015-10-01 Broke LTC3 KiCad symbol library into separate libs for each component.
2015-10-01 Added more KiCad symbol libraries; updated schematic accordingly.
    Nothing we didn't already have in the cache lib. I just wanted to
    make sure we had discrete copies.
    [Launch_Tower_Computer_III.sch, beaglebone_cape.sch, dcdc_converter.sch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]
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2015-10-20 Progress on merging master with Charging_Circuit branch.
    Still have plenty of schematic clean-up to perform. There's a lot
    going on around the LT8490.
    [battery_mgmt.sch, power_sources.sch]
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2015-10-25 Fixed LTC3 battery spec in design doc.
    Using an 8s2p cofiguration, not 8s1p.
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2015-11-01 Deleted "Power Sources" sheet.
    Moved what little circuity it contained into the "Battery Charging"
    and "Battery Balancing" sheets.
    [Launch_Tower_Computer_III.sch, battery_balance.sch, battery_mgmt.sch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]
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2015-11-04 Finished cleaning up battery management (LT8490) schematic.
    High probability of errors, and certainly still room for improvement,
    but I want to get the work on this branch merged back to the trunk.
    [battery_balance.sch, battery_mgmt.sch]
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2015-11-04 Fixed inter-sheet connections.
    We still need to think about the connection scheme between the battery
    management circuit, the battery balancing circuit, and the DC/DC
    converter circuits.
    [Launch_Tower_Computer_III.sch, battery_balance.sch]
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2015-11-16 LTC3: ignition control adjustments.
    1. Renamed "Ignition Control" sheet to "Rocket Interface". Rocket I/O
    connectors will appear on this sheet.
    2. Other minor adjustments to ignition control schematic (signal
    labels, etc.).
    3. Added a datasheet for the ignition control circuit's schmitt
    inverter.
    [Launch_Tower_Computer_III.sch, battery_balance.sch, battery_mgmt.sch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]
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2015-11-21 LTC3: Schematic corrections.
    1. Replaced ignition schematic Schmitt trigger symbols with symbols
    that actually include the Schmitt squiggle.
    2. Annotated DC detection circuit on battery management schematic;
    removed related entry from TODO list.
    [Launch_Tower_Computer_III.sch, battery_balance.sch, battery_mgmt.sch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]
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2015-12-12 Cleaned up trigger schematics and fixed some resistor values.
    [rocket_interface.sch]
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2015-12-16 LTC3: Progress on rocket/ignition schematic.
    1. Fixed mis-wired relay diodes.
    2. Completed ignition relay circuitry.
    3. Began work on umbilical connector circuitry.
    [Launch_Tower_Computer_III.sch, rocket_interface.sch]
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2015-12-22 Added note section to heirarchical schematics. Added path to ground on DC-DC converters. Replaced thermistor with 'duct tape' 0 ohm resistor on BQL77PL900.
    [Launch_Tower_Computer_III.sch, battery_balance.sch, dcdc_converter.sch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]
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2015-12-23 LTC3: Fixed reversed input "OR" diodes on battery charging schematic.
    [battery_mgmt.sch]
2015-12-29 LTC3: Began replacing Schottky OR diodes w/ "ideal" diodes.
    Created schematic symbol for TI LM74610-Q1 ideal/smart diode
    controller. Added relevant data sheets.
    Began implementing the circuitry that will replace the existing
    Schottky input diodes in the battery charging schematic. Left my work
    off to the left hand side of the page. Still need to complete and
    integrate with the charging circuitry.
    Also added a TODO item to the DC/DC converters schematic.
    [Launch_Tower_Computer_III.sch, battery_balance.sch, battery_mgmt.sch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]
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2016-01-09 LTC3: Replaced LM74610 ideal diodes on power input with Picor PI2127.
    Simpler to use; more than enough current capacity (12A).
    [Launch_Tower_Computer_III.sch, battery_balance.sch, battery_mgmt.sch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]
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2016-01-30 LTC3: Replaced thermistor/0R on charger and balance schematics w/ connector.
    Each to be connected to an off-board NTC thermistor taped to the
    battery pack.
    [Launch_Tower_Computer_III.sch, battery_balance.sch, battery_mgmt.sch]
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2016-01-30 LTC3: Minor progress on ignition schematic.
    1. Corrected BBB ROCKET_READY signal (prefixed w/ slash to indicate
    active-low).
    2. Added explanatory note to ignition schematic's "Input Logic" block.
    3. More TODOs, comments added to schematic; more questions added to
    DESIGN_REVIEW_QUESTIONS list.
    4. Updated schematic PDF.
    [Launch_Tower_Computer_III.sch, battery_balance.sch, battery_mgmt.sch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]
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2016-02-10 LTC3: Replaced 2-cell battery symbol with 1-cell symbol.
    [Launch_Tower_Computer_III.sch, battery_balance.sch, battery_mgmt.sch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]
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2016-02-19 LTC3: Replaced external device and power PPTCs w/ fuses.
    [Launch_Tower_Computer_III.sch, battery_balance.sch, battery_mgmt.sch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]
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2016-02-19 LTC3: Standardized optoisolator selection.
    Replaced the Avago 4N35 on the ignition control schematic with the
    Toshiba TLP3542 used on the external power and triggers schematic.
    This reduces the number of unique parts used in the design. The Avago
    has an order of magnitude faster switching time than the Toshiba, but
    that shouldn't matter for the ignition control circuit; the Toshiba's
    2.5A max current is way more than sufficient.
    [external_devices.sch, rocket_interface.sch]
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2016-03-11 LTC3: Costmetic maintenance, etc.
    1. Prettified external device power and triggers sheets.
    2. Fixed order of sub-sheets within schematic.
    3. Updated PDF of schematic.
    [Launch_Tower_Computer_III.sch, battery_balance.sch, battery_mgmt.sch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]
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2016-04-02 LTC3: Fixed mis-oriented diodes in battery management schematic.
    [battery_balance.sch]
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2016-04-09 LTC3: Changes to Lab Supply Detection Circuit
    - Replaced NPN with an NMOS for simpler design
    - Changed voltage divider on the gate of the NMOS
    [battery_mgmt.sch]
2016-04-10 LTC3: More component values and footprint assignments.
    Split the two-in-one Beagle Bone expansion header component into two
    separate components. Otherwise, we'd be stuck with having to use a
    single footprint for the BB cape pin headers, which means pin
    numbering that doesn't match the BB docs.
    [Launch_Tower_Computer_III.kicad_pcb, Launch_Tower_Computer_III.sch, battery_balance.sch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]
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2016-04-16 Created N_MOS_SOT_26 Schematic symbol. Fixed pin numbering on SOT 26.
2016-04-16 LTC3: Work on batt. mgmt., ignition control schematics.
    1. Specified part number and footprint for Zener diodes in battery
    management schematic.
    2. Specified footprint for input detection MOSFET in battery
    management schematic.
    3. Replaced shorting bar with connector in ignition control schematic.
    (Shorting bar is panel mounted, not on PCB.)
    Also updated schematic annotations, and generated fresh netlist.
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2016-04-16 LTC3: Minor fixes to test points in batt. balance schematic.
    Also updated netlist, schematic PDF.
    [Launch_Tower_Computer_III.sch, battery_balance.sch, battery_mgmt.sch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]
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2016-05-03 LTC3: More schematic style policing and prettification; a few fixes.
    1. Cleaned up the DC-DC converter sheet. Fixed the broken manual
    override switching of the converters; copied the style on the external
    power and trigger sheets.
    2. Added +3.3V power node to charge management sheet, connected to the
    LT8490's LDO33 pin. The DC-DC converters use this as their enabling
    signal.
    3. Fixed broken FET symbols on charge management (LT8490) sheet.
    [Launch_Tower_Computer_III.sch, battery_balance.sch, battery_mgmt.sch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]
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2016-05-08 LTC3: Fixes, clean-ups...
    1. Removed inverters from DC-DC converters' INHIBIT pin circuitry.
    Renamed node labels accordingly.
    2. Moved zero-volt charging FET on bq sheet. It was wired to bypass
    the discharge FETs, and should be bypassing the charge FETS.
    3. Added connectors between board and igntion external interfaces
    (breaker, arming switch, shorting bar, ignition power).
    4. Finished BakerCon indicator.
    [Launch_Tower_Computer_III.sch, battery_balance.sch, battery_mgmt.sch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]
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2016-05-09 LTC3: Redesigned BAKERCON indicator.
    Reduced the LED count from six to three. LEDs are all powered from
    the 5V supply, driven by FETs switched by the appropriate ignition
    sub-system signals.
    [Launch_Tower_Computer_III.sch, beaglebone_cape.sch, cell_protection.sch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]
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2016-05-11 LTC3: Minor Power Management Changes to LT8490
    -replaced 600 ohm resistor on ideal diode with 0 ohm resistor
    -selected transistors for feedback resistor disconnect subcircuit
    [Launch_Tower_Computer_III.sch, beaglebone_cape.sch, cell_protection.sch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]
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2016-05-12 LTC3: More footprint assignment.
    Set footprint to "OFF-BOARD" for all off-board components. This
    results in an error dialog when opening the footprint assignment tool,
    but it makes it obvious which components shouldn't have any footprint
    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
    [Launch_Tower_Computer_III.sch, beaglebone_cape.sch, cell_protection.sch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]
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2016-05-31 LTC3: Corrected PTN78020[WH] footprint.
    [Launch_Tower_Computer_III.kicad_pcb]
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2016-06-08 LTC3: Fixed incorrect pin number on bq77PL900 footprint.
    Pin 48 was labelled as pin 49.
2016-06-08 LTC3: Made use of corrected bq footprint.
    [cell_protection.sch]
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2016-06-14 LTC3: Finished up PCB layout of DC-DC converters (mostly).
    Still need to finish wiring up the LTC2991 sensor IC. Current shunt
    resistors need work: either replace their schematic symbol with a
    standard resistor, or replace their PCB footprints with a 4-terminal
    SMT device.
    [Launch_Tower_Computer_III.kicad_pcb]
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2016-06-16 LTC3: Fixed mis-named pin in VIN power node symbol.
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2016-06-29 LTC3: Deleted ancient, orphaned DC-DC converter schematic files.
    Not sure how those slipped by unnoticed for so long.
    [dcdc_converter_19v.sch, dcdc_converter_5v.sch]
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2016-06-30 LTC3: Charge Controller Layout
    With boards broken up, charge controller circuitry has been re-layed out.
    This commit is a rough first pass - there is no via stiching to ground
    yet.
    [LTC3_Cell_Protection.sch, LTC3_Charge_Controller.kicad_pcb, LTC3_Charge_Controller.sch]
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2016-07-09 LTC3: Selected parts, footprints for power connectors on charge controller board.
    Also corrected footprints for STATUS and FAULT LEDs.
    [LTC3_Charge_Controller.sch]
2016-07-09 LTC3: Reworking Charge Controller Layout
    - Assigned correct footprints to LEDs, Fuse, output connector
    - Reworked high current polygons
    - Added mounting holes
    Still more work to be done.
    [LTC3_Cell_Protection.kicad_pcb, LTC3_Charge_Controller.kicad_pcb]
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2016-07-16 LTC3: More BOM work; fixed Vbatt test point on schematic.
    Somehow there were two test points on top of each other.
    [LTC3_Charge_Controller.sch]
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2016-07-21 LTC3: Main Board Layout con't
    For the most part finished a layout of the main LTC3 board! Hooray!
    Had to adjust a symbol and hoping that it doesn't mess up the library.
    Todo: Figure out of this is 4 layer or 2 layer board. May be doable as 2.
    [LTC3.kicad_pcb, LTC3.sch, beaglebone_cape.sch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]
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2016-08-31 LTC3: Corrections, BOM progress on Cell Protection.
    1. Moved LTC2990's current-sense shunt resistor from the "battery" side
    to the "pack" side.
    2. Turned the two-terminal off-board I2C connector into a
    four-terminal connector that brings in +5V from the LTC board (instead
    of taking +5V from the bq IC).
    3. Corrected mis-wired shunt resistor for bq IC. SRPGND and SRPGND
    were connected to the wrong (opposite) sides of the shunt resistor.
    4. Progress on BOM (shopping for orderable parts).
    [LTC3_Cell_Protection.sch, LTC3_Cell_Protection.xlsx]
2016-09-04 LTC3: Replaced DC-DC converters' individual switches with a single switch.
    One main power switch now enables all three converters.
    Added pin header to each converter's nINHIBIT pin to facilitate manual
    control.
    [LTC3.sch, beaglebone_cape.sch, dcdc_converter.sch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]
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2016-09-04 LTC3: Modified LTC external triggers schematic.
    Replaced breakers with 100 ohm current-limiting resistors.
    [beaglebone_cape.sch, dcdc_converter.sch, external_power.sch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]
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2016-09-04 LTC3: Modified LTC BeagleBone cape schematic.
    Replaced external I2C connector with combined I2C/5.0V connector.
    Added a second connector in parallel, so that the charge controller
    and cell protection boards each have their own.
    [beaglebone_cape.sch, external_triggers.sch]
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2016-09-06 LTC3: Corrected charge controller shunt resistor BOM data.
    Really done this time, for reals.
    [LTC3_Charge_Controller.sch, LTC3_Charge_Controller.xlsx]
2016-09-06 LTC3: One last correction to charge controller BOM.
    And I'm serious this time.
    [LTC3_Charge_Controller.sch, LTC3_Charge_Controller.xlsx]
2016-09-06 LTC3: Corrected LTC2990 shunt resistor spec, etc.
    I was only kidding about being finished.
    [LTC3_Charge_Controller.sch, LTC3_Charge_Controller.xlsx]
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2016-09-07 LTC3 Cell Protection Layout
    Reworked layout with changes to schematic and various footprints.
    Also added via stapling.
    [LTC3_Cell_Protection.kicad_pcb, LTC3_Cell_Protection.sch]
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2016-09-07 LTC3: LTC schematic changes; LTC BOM work.
    * Replaced LTC external power and trigger circuits' off-board manual
    override switches with board-mounted tactile momentary switches.
    Simplifies assembly, and should be more than adequate for debugging
    purposes.
    * Changed cell protection diodes D1 and D6 from Rohm 1SS355 to ComChip
    CDSU4148. CDSU4148 is already used on the LTC board, and is higher
    spec than the 1SS355.
    [LTC3.sch, LTC3.xlsx, LTC3_Cell_Protection.xlsx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]
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2016-09-08 LTC3: Modified Cell Protection schematic, correcting R4 value.
    No impact to PCB layout.
    [LTC3_Cell_Protection.sch, LTC3_Cell_Protection.xlsx]
2016-09-08 LTC3: Modified LTC schematic.
    Replaced ST Micro 74V1G08CTR single, two-input AND gate with a TI
    SN74AHC1G08 (also a single, two-input AND gate). This required a
    footprint change, so it will impact the PCB layout.
    [LTC3.sch, LTC3.xlsx, beaglebone_cape.sch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]
2016-09-08 LTC3: Modified LTC BOM, schematic.
    1. Added footprints for mechanical relays. (PCB layout already had
    correct footprint; but incorrect annotation.)
    2. Created footprint for RJ-45 jack. This impacts the existing PCB
    layout.
    [LTC3.kicad_pcb, LTC3.xlsx, rocket_interface.sch]
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2016-09-09 LTC3 Layout Changes to Charge Controller/Cell Balancing
    Finished up some changes on charge controller/cell balancing layout.
    DRC gives zero errors, and everything is connected, huzzah!
    [LTC3_Cell_Protection.kicad_pcb, LTC3_Cell_Protection.sch, LTC3_Charge_Controller.kicad_pcb]
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2016-09-13 LTC3: LTC BOM and PCB changes.
    1. Added RJ45 connector outline to BeagleBone footprint.
    2. Rotated BeagleBone footprint on PCB, so that the RJ45 connector
    is on a board edge.
    3. Added a notch to the board for BeagleBone RJ45 jack clearance.
    4. Updated PCB footprint annotations to align with changes made to the
    LTC schematic in the past few months.
    5. Changed BAKERCON MOSFETs to be same part used to activate ignition
    relays. (Fewer distinct components on the board.)
    [LTC3.kicad_pcb, LTC3.sch, LTC3.xlsx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]
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2016-09-15 LTC3: Final Layouts & Gerbers
    Reworked the power section on the LTC board (I did this previously with
    small traces, now uses polygons).
    At this point, all layout work should be finished and the boards should
    be ready to be shipped off.
    I've uploaded new gerbers of each of the boards into
    ltc3/compiled/gerbers_9_15_2016. Old gerbers can be found in
    ltc3/compiled/gerbers_OLD.
    [LTC3.kicad_pcb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]
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2017-02-09 LTC3: Minor PCB adjustments; generated fresh Gerbers.
    1. Nudged board outlines outward ~1mm to allow for clearance between
    copper fill zones and board edge.
    2. Standardized layer names.
    2. Generated fresh Gerbers for each board. New files have distinct,
    Protel-style extensions, just the way OSH Park likes it.
    [LTC3-B.Cu.gbl, LTC3-B.Mask.gbs, LTC3-B.Paste.gbp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]
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2019-03-08 Replaced old schematic PDFs with new KiCad v5 versions.
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

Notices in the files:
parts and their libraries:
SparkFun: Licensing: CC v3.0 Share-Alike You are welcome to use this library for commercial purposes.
